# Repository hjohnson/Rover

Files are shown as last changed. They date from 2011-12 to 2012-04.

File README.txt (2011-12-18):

Introduction:
      This time, I'm presenting a whole robot, a project that has a slightly larger scale than my normal ones. This robot (or rover) was designed as an educational tool, a project to be built by teams of High School students over a period of 2-3 weeks. ÊAs such, the robot was designed for simplicity and durability, not low price. The robotÕs design is split into several modules: Mechanical Frame, Locomotion, Sensors, and Control. 

Mechanical Frame: 
	Material: The frame is constructed from four 1Ó width 80/20 extruded aluminum rails. For those who donÕt know, the 80/20 T-slot system is called Òthe industrial erector set,Ó and the description is fitting. The rails can be cut to size relatively easily with hand tools (though we use power tools,) and can be bolted together using aluminum plates, ÒT-nutsÓ and screws, instead of welding. This means that the system is easily reconfigurable on the fly, and small mistakes can be quickly remedied by loosening the plates and shifting the rail, instead of by removing welds.  
	Design: The main frame is a simple rectangle constructed from four lengths of 80/20 rail, bolted together at the corners with four triangular plates.  Attached to this main frame are several other lengths of rail. One houses the bumper; another houses the ball transport and vulnerability switch. (All of which will be discussed later) Three vertical stalks are also integrated into the design to hold other sensors. As a side bonus, these stalks are mounted firmly enough that the robot can technically be flipped upside down and rest on them, for easier service.

Locomotion:
	Mechanical Drive System: The robot incorporates two pneumatic wheels with integrated sprockets. The two wheels can rotate independently of each other, enabling steering, and are attached to a single axle, which is a 1/2-inch outside diameter tube. This axle is attached to the underside of the frame using pillow blocks.  Two 8-amp stepper motors drive the 2 wheels through a chain system. Sprockets attach to the motorsÕ drive shafts, and connect to the wheel-mounted sprockets through lengths of chain.  
	Motor Control System: A pair of Anaheim Automation MBC10101 Stepper Motor Drivers control the stepper motors. These drivers are powered by 24V provided by the robotÕs power unit, and have control inputs driven by the main control card. The main controls are: clock input, to determine the speed of the motors; Inhibit, to remove power from the motors and stop the robot; and Direction, to control the direction of rotation. These inputs are controlled by the main board, which will be discussed later. These drivers, while expensive, are from my experience highly reliable and are hard to burn, an excellent feature when wired by inexperienced builders who can easily miss a ground or clock signal. 
	Electrical Supply (power unit): The robotÕs power is provided by a custom supply based around two 12V, 2200mAh, Lead-Acid rechargeable batteries. When in Charge mode, the power supply wires these two batteries in parallel, each with their own 10 ohm ceramic power resistor, to the main power jack. While in this mode, ~14V can be supplied from an external regulated supply to charge the batteries. When in Drive mode, the power supply switches the two batteries into series, providing 24V output to the main power jack, which runs to the stepper motor drivers. The power supply also taps one of the batteries to supply 12V to a 7805 5V voltage regulator, which powers the control circuitry. Due to the power dissipation through this 7805, it is screwed to a Òheat sinkÓ (bottle cap). 

Sensors:
	The robot integrates several sensors to react to its surroundings. These include front-mounted bumper switches and phototransistors, and a rear-mounted vulnerability switch. 
	Bumper: A flexible bumper is attached to the front of the robot, along with 2 momentary lever switches. This enables the robot to detect when it has run into an object, usually the wall. The robotÕs response to this information can be determined in software by the students.
	Vulnerability Switch: A 3 position (SPTT) toggle switch is mounted to the rear of the robot, and acts as a manual shutdown switch and Òweak spot.Ó When the switch is positioned in the center (not connected), the robot operates normally. However, when the switch is actuated to either side, the robot instantly shuts down, turning off the motors and rendering the robot inoperable. This feature is implemented in software, but tampering with that section of code is forbidden. This switch is primarily used as a safety feature, but is also exploited for the high school competition, as bonus points are awarded to teams who can activate their opponentsÕ switches. 
	Phototransistors: While these are not currently attached, the phototransistors can be used to detect light levels, allowing the robots to navigate based on guidance from a flashlight, as well as to seek out the beacons above the competitionÕs Ògoals.Ó 

Control:
	At last, the more recognizable part. The robotÕs control system is remarkably simple, consisting of an Arduino-based card and an associated remote control.
	Control Card Hardware: 
      The actual circuitry on the card is remarkably simple, and primarily consists of an Arduino microprocessor, an XBee wireless transceiver, and some support circuitry.
       Motor Control: The Arduino output pins are buffered through 74LS14 hex inverters and then sent to the stepper motor drivers and the inputs from the bumper and vulnerability switches. The outputs are pulled up through resistors to 5V to ensure that the drivers are properly driven, as we had previously encountered problems where the ArduinoÕs output pins couldnÕt sufficiently drive the motor driversÕ input pins. 
      Sensors: The sensor inputs are buffered as well to form an extremely simple debouncing circuit. The Phototransistors also run through 1.5K resistors to ground, forming common collector amplifiers whose outputs run into the Analog In pins on the Arduino. 
      XBee: The control card utilizes an XBee wireless transceiver to enable bidirectional serial communication between the robot and the remote control. An Adafruit XBee Adapter kit is used to house the XBee and convert the ArduinoÕs 5V logic to the XBeeÕs 3.3V logic.  
	Control Card Software: 
      Motor Control: The top of the CardÕs priority list is controlling the motor drivers. Each of these drivers takes 3 inputs (clock, inhibit, and direction) as discussed previously. The 2 clock lines are driven by independent square waves generated by the Arduino Tone library. These square waves typically have frequencies between 2KHz and 5KHz.  Because the stepper motors have 200 steps/rotation, these speeds translate to motor speeds between 10 and 25 motor revolutions per second. However, due to the gearing present through the sprockets, the robotÕs wheels rotate at a lesser rate. (Embarrassingly, I havenÕt actually counted sprocket teeth or done the rest of this math yet. IÕll get back to you.) Inhibit and Direction, the other 2 data lines (per driver) are comparatively simple. When the driver sees a logic low on the inhibit pin, the motor is turned on, and when the driver sees a logic high, the motors are turned off. Similarly, for direction, logic low results in forward rotation, logic high results in backwards rotation. 
      Vulnerability Switch: The vulnerability switch input is monitored using an interrupt, whose interrupt service routine disables both motors, then waits for the vulnerability switch to be returned to center before exiting. In this way, the motors are disabled upon the switch being flicked, and will not re-enable, no matter what the user says, until the switch is returned to center.
      XBee Remote Control: To communicate through the XBee, a simple serial protocol is used, along with a pre-determined command set. Incoming serial bytes are read and interpreted by the program, with, for example, ÒWÓ signifying forward movement, ÒSÓ signifying backward movement, and ÒFÓ signifying stop. For more information about this process, look at the previous article, about the Remote Control designed to interface with this system.

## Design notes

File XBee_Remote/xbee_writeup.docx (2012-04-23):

This is a custom XBee-based remote control. The remote uses a 7-segment display, 7 buttons (plus a reset button), and 6 analog inputs as a user interface, and a 6-pin FTDI header for reprogramming through the Arduino IDE. Default code includes a program that prints the current state of the buttons to the XBee and a program that uses a switch statement to select what to send based on the buttons being pressed.

I originally designed this board for the Summer@Brown education program. In a class for this program, students design, construct, and program an aluminum-framed robot, and compete with it in a basic navigational challenge. Students have the option of controlling their robots remotely for part of the exercise. Previously, the control systems of these robots were created using discrete gates on 7400 series logic chips, and the remote control functionality was provided by expensive RF demo boards from Texas Instruments. I decided to upgrade the systems by implementing an Arduino and XBee based control system on the robots. That way, the robots could be controlled by anything that could speak over a serial connection. I had the students build their own remote controls on a breadboard, but quickly found that the wires would pop out and the systems would break. To fix the problem, I designed this remote control. Students would still solder it together and program it, but it would be easier to hold, have more buttons, and be more reliable. Further, it would be expandable: If they outstripped the 7 switches, they could always attach more switches, potentiometers, or I2C communications devices through the analog lines.

While I designed this board to be paired with a control system mounted on a robot, it can be used to interface with anything that communicates over an XBee serial connection. As such, it could work as both a remote control and a remote monitoring system. The Atmega328P runs off 5 volts, while the XBee runs of 3.3 volts. To convert between the two, a low drop out regulator is used, along with a 74AHC125 buffer. However, the '125 has another useful feature. Using its active-low Output Enable pin, its outputs switched to High Impedance at will. Since the buffer is used on both the RX and TX lines, the Atmega328P can disconnect itself from the XBee.

Typically, when Arduinos and XBees are combined, the XBee cannot be connected to the Arduino during serial bootloading. To solve this problem, designers usually put in a DPDT switch to manually transition between connecting the Atmega328 to the computer and connecting it to the outside world. However, since the Atmega I/O lines are high impedance during reset and bootloading, I simply connect the ‘125 Output Enable pin to the Atmega, and install a pull-up resistor on the line. This means that during bootloading, the Atmega is disconnected from the XBee. When the program is loaded and the Atmega is ready to communicate wirelessly, it simply pulls the Output Enable pin low.

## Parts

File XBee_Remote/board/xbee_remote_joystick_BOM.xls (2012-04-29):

Digi-Key Part Number | Manufacturer | Manufacturer Part Number | Quantity 1 | Description | Comments
ATMEGA328-PU-ND | ATMEL | ATMEGA328-PU | 1 | IC MCU AVR 32K FLASH 28PDIP
568-1393-5-ND | NXP SEMICONDUCTORS | 74HC125N,652 | 1 | IC BUFFER DVR TRI-ST QD 14PDIP
568-1484-5-ND | NXP SEMICONDUCTORS | 74HC595N,112 | 1 | IC SHIFT REGISTER 8BIT 16DIP
296-21633-5-ND | TEXAS INSTRUMENTS | UA78M33CKCS | 1 | IC POS-V REG 500MA 3.3V TO220-3 | 3.3V regulator
160-1708-ND | LITE-ON INC | LTL-1CHE | 2 | LED 3MM HI-EFF RED DIFFUSED
X908-ND | ECS INC | ZTT-16.00MX | 1 | CER RESONATOR 16.00MHZ
150QBK-ND | YAGEO | CFR-25JB-52-150R | 2 | RES 150 OHM 1/4W 5% CARBON FILM | Can swap resistors, caps for generics, etc
1.0KQBK-ND | YAGEO | CFR-25JB-52-1K | 1 | RES 1.0K OHM 1/4W 5% CARBON FILM
10KQBK-ND | YAGEO | CFR-25JB-52-10K | 3 | RES 10K OHM 1/4W 5% CARBON FILM
399-4151-ND | KEMET | C315C104M5U5TA | 3 | CAP CER 0.1UF 50V 20% RADIAL
P966-ND | PANASONIC - ECG | ECE-A1CKS100 | 1 | CAP ALUM 10UF 16V 20% RADIAL
P5165-ND | PANASONIC - ECG | ECA-1VM101 | 1 | CAP ALUM 100UF 35V 20% RADIAL
A98036-ND | TE CONNECTIVITY AMP | 1776275-2 | 1 | TERM BLOCK 2POS SIDE ENT 3.5MM
A26509-40-ND | TE CONNECTIVITY AMP | 4-103741-0 | 1 | CONN HDR BRKWAY .100 40POS VERT
S5751-10-ND | SULLINS CONNECTOR SOLUTIONS | NPPN101BFCN-RC | 2 | CONN RECEPT 2MM SINGLE STR 10POS | Xbee headers
EG1903-ND | E-SWITCH | EG1218 | 1 | SWITCH SLIDE SPDT 30V.2A PC MNT
EG2513-ND | E-SWITCH | TL1107BF180WQ | 7 | SWITCH TACTILE SPST-NO 0.05A 12V
In addition:
Sparkfun 7-segment, COM-08546
Sparkfun Thumb Joystick, COM-09032

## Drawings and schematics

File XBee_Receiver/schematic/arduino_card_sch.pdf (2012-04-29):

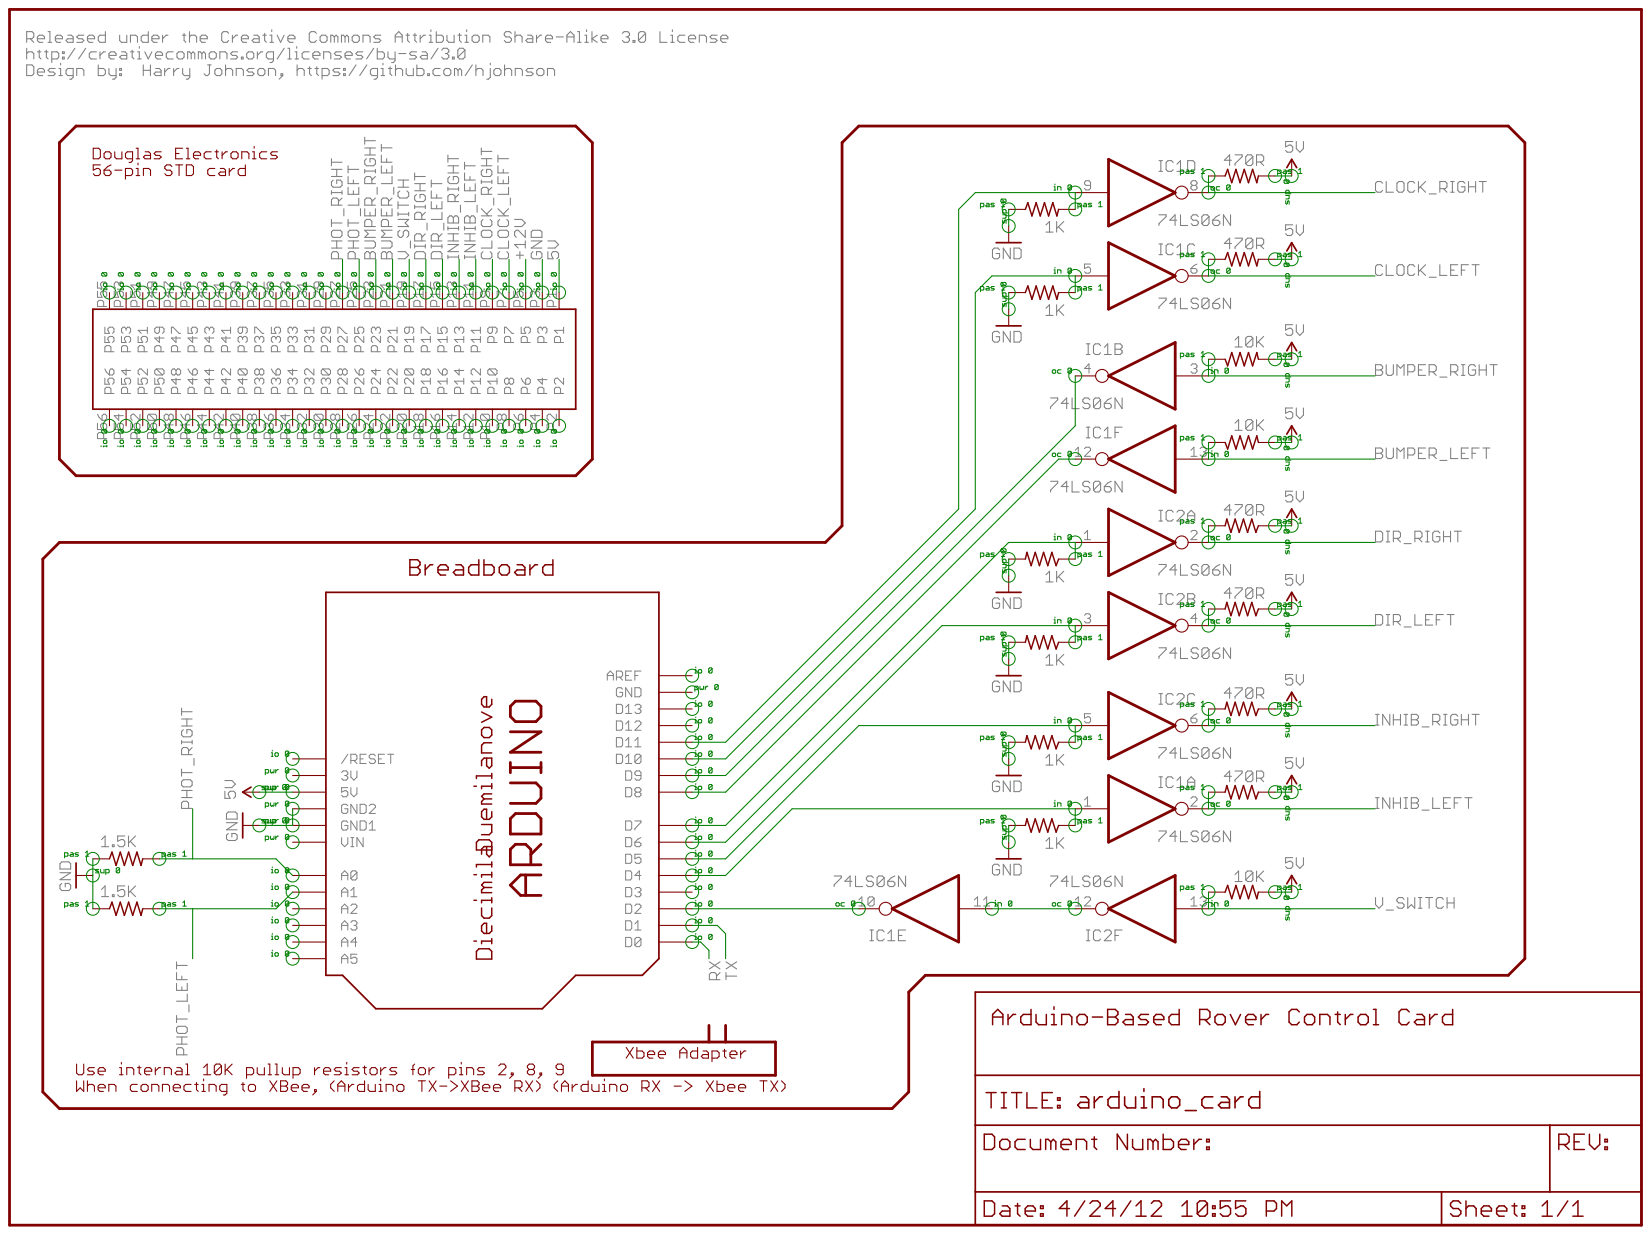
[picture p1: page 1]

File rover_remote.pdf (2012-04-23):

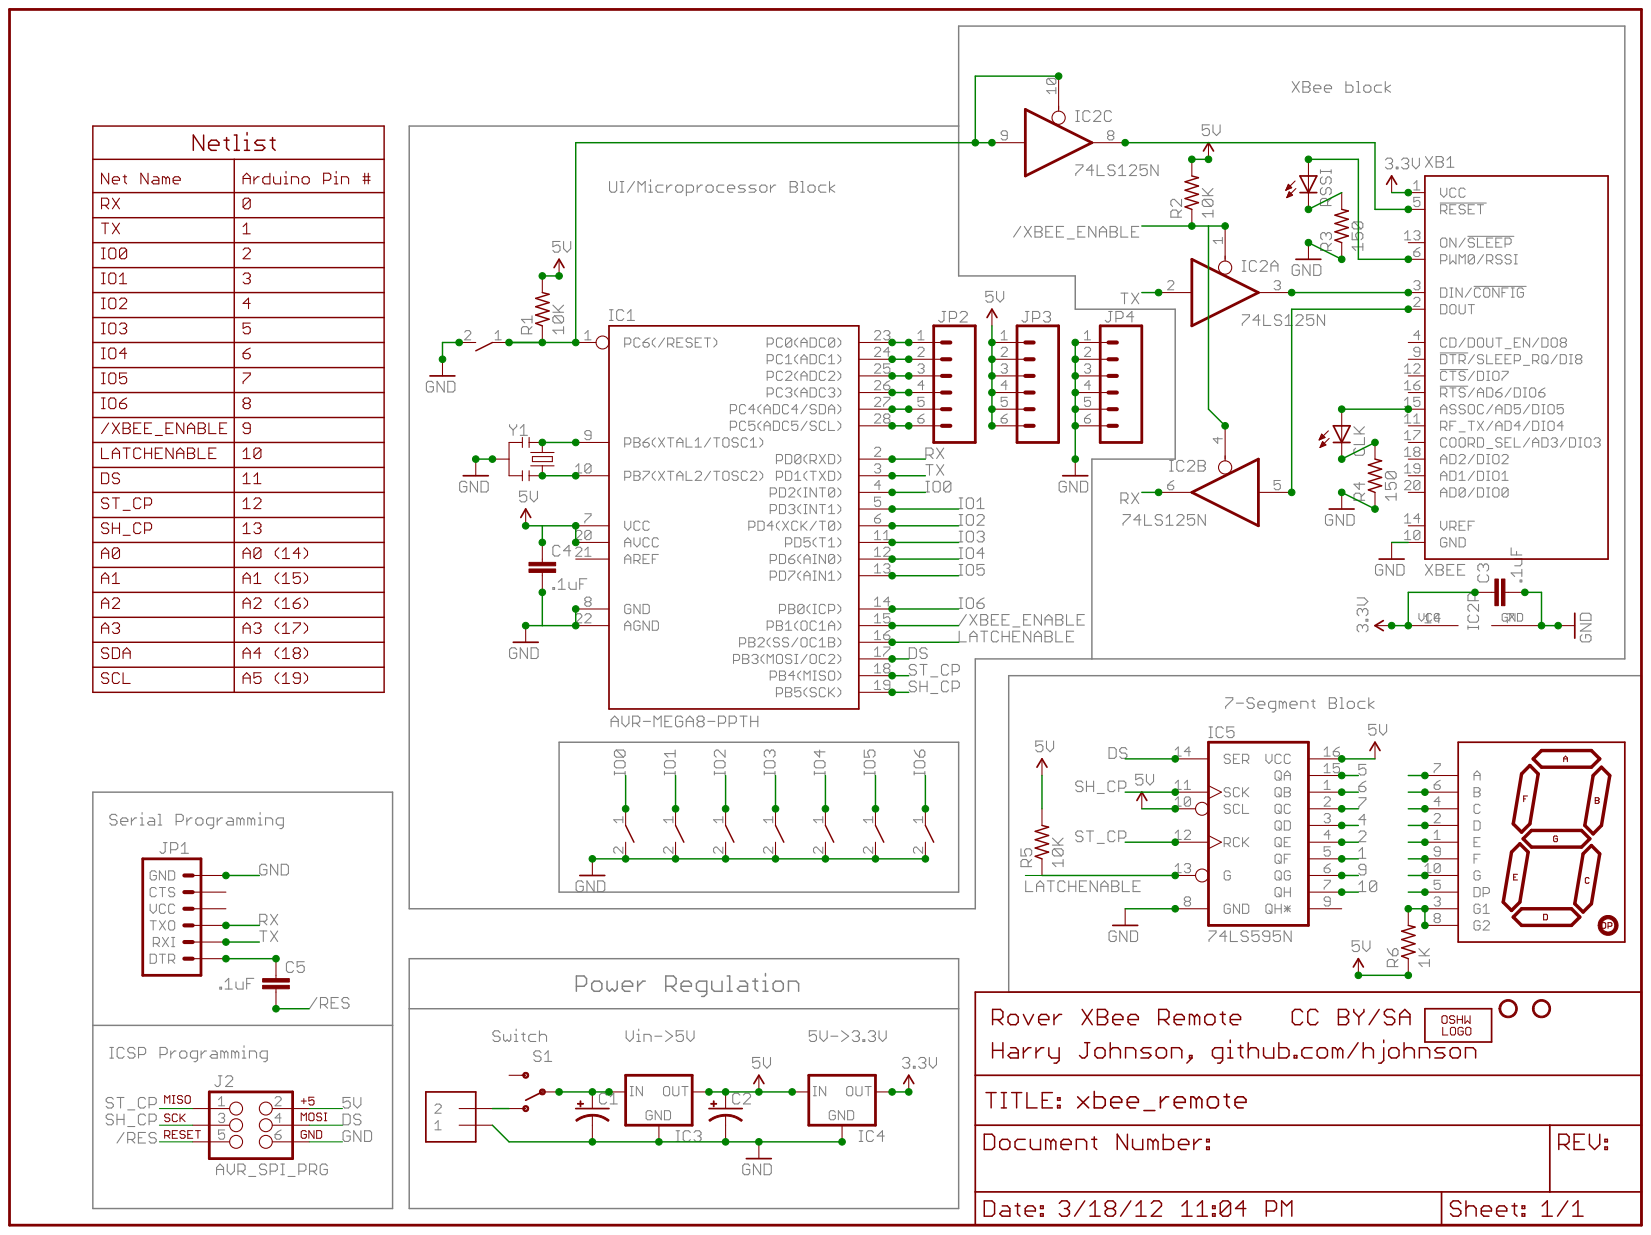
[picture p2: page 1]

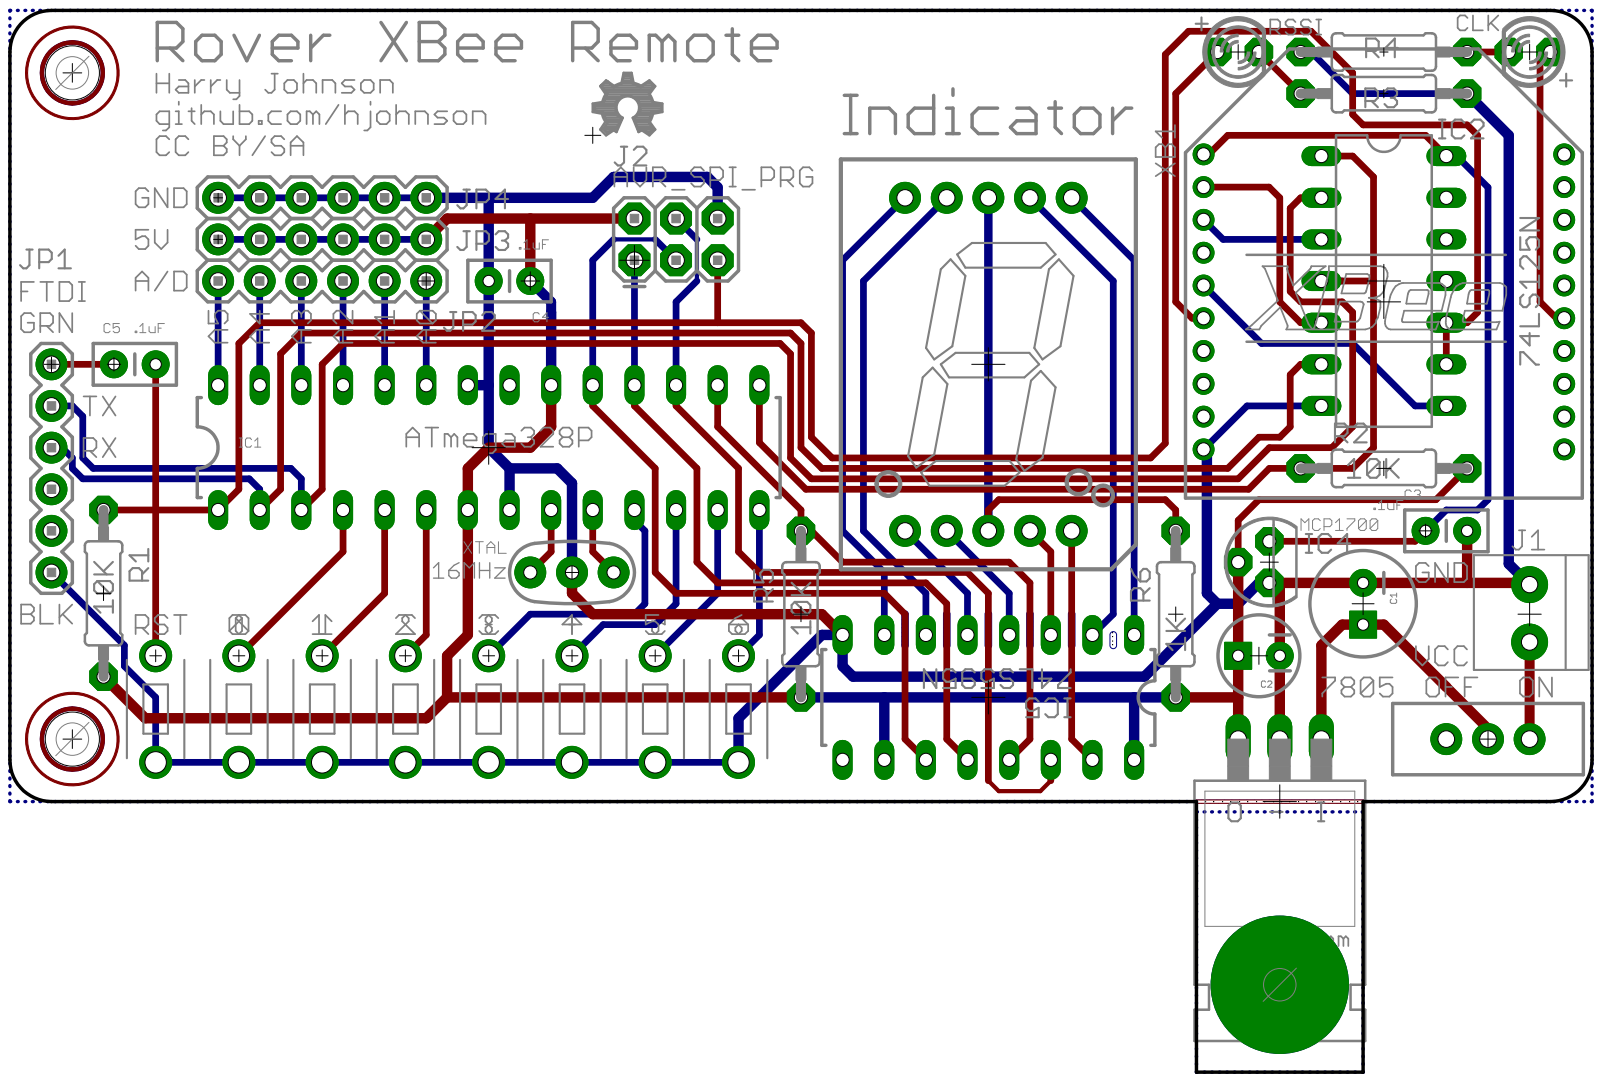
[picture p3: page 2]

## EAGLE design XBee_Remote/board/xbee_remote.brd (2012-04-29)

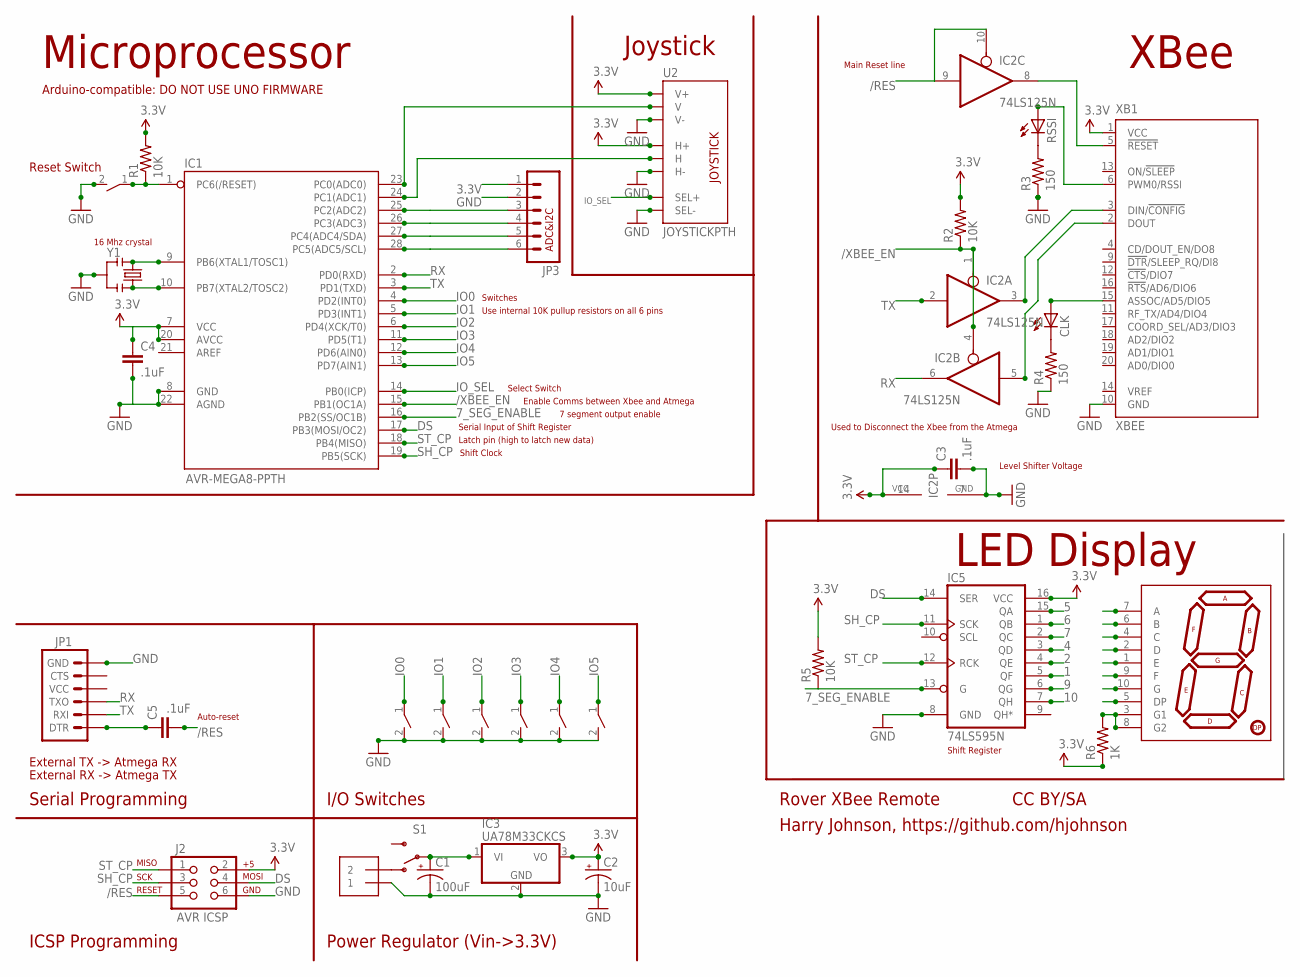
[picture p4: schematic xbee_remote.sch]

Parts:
C1: 100uF; CPOL-RADIAL-100UF-25V
C2: 10uF; CPOL-RADIAL-10UF-25V
C3, C4, C5: .1uF; CAP-PTH-SMALL2
CLK: LED3MM
IC1: AVR-MEGA8-PPTH; DIL28-3
IC2: 74LS125N; DIL14
IC3: UA78M33CKCS; TO220V
IC5: 74LS595N; DIL16
J1: 1X2-3.5MM; 3.5MMTERM
J2: AVR ICSP; 2X3
JP1: ARDUINO_SERIAL_PROGRAMPTH; 1X06
JP3: M06SIP; 1X06
R1, R2, R5: 10K; 0207/10
R3, R4: 150; 0207/10
R6: 1K; 0207/10
RSSI: LED3MM
S1: SWITCH-SPSTPTH; SWITCH-SPDT
U2: JOYSTICKPTH; JOYSTICK
U$4: 7-SEGMENT-DISPLAY-1"-RED; 7-SEGMENT-1"PTH
U$8, U$9, U$10, U$11, U$12, U$13, U$14: TACT_TL1107
XB1: XBEE
Y1: RESONATORPTH; RESONATOR-PTH

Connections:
1: IC5.5 (QF), U$4.1 (E)
2: IC5.4 (QE), U$4.2 (D)
3.3V: C2.1 (+), C3.1, C4.1, IC1.7 (VCC), IC1.20 (AVCC), IC2.14 (VCC), IC3.3 (VO), IC5.16 (VCC), J2.2, JP3.1, R1.2, R2.2, R5.2, R6.1, U2.H1 (H+), U2.V1 (V+), XB1.1 (VCC)
3V3_/RST: IC2.8 (O), XB1.5 (!RESET)
3V3_RX: IC2.5 (I), XB1.2 (DOUT)
3V3_TX: IC2.3 (O), XB1.3 (DIN/!CONFIG)
4: IC5.3 (QD), U$4.4 (C)
5: IC5.15 (QA), U$4.5 (DP)
6: IC5.1 (QB), U$4.6 (B)
7: IC5.2 (QC), U$4.7 (A)
7_SEG_ENABLE: IC1.16 (PB2(SS/OC1B)), IC5.13 (G), R5.1
9: IC5.6 (QG), U$4.9 (F)
10: IC5.7 (QH), U$4.10 (G)
/RES: C5.2, IC1.1 (PC6(/RESET)), IC2.9 (I), IC2.10 (OE), J2.5, R1.1, U$8.1
/XBEE_EN: IC1.15 (PB1(OC1A)), IC2.1 (OE), IC2.4 (OE), R2.1
A2: IC1.25 (PC2(ADC2)), JP3.3
A3: IC1.26 (PC3(ADC3)), JP3.4
DS: IC1.17 (PB3(MOSI/OC2)), IC5.14 (SER), J2.4
GND: C1.2 (-), C2.2 (-), C3.2, C4.2, IC1.8 (GND), IC1.22 (AGND), IC2.7 (GND), IC3.2 (GND), IC5.8 (GND), J1.1, J2.6, JP1.6 (GND), JP3.2, R3.1, R4.1, U2.B2A (SEL-), U2.H3 (H-), U2.V3 (V-), U$8.2, U$9.2, U$10.2, U$11.2, U$12.2, U$13.2, U$14.2, XB1.10 (GND), Y1.2
IO0: IC1.4 (PD2(INT0)), U$9.1
IO1: IC1.5 (PD3(INT1)), U$10.1
IO2: IC1.6 (PD4(XCK/T0)), U$11.1
IO3: IC1.11 (PD5(T1)), U$12.1
IO4: IC1.12 (PD6(AIN0)), U$13.1
IO5: IC1.13 (PD7(AIN1)), U$14.1
IO_SEL: IC1.14 (PB0(ICP)), U2.B1A (SEL+)
unnamed: IC1.9 (PB6(XTAL1/TOSC1)), Y1.1
unnamed: IC1.10 (PB7(XTAL2/TOSC2)), Y1.3
unnamed: J1.2, S1.1 (O)
unnamed: C5.1, JP1.1 (DTR)
unnamed: R6.2, U$4.3 (G1), U$4.8 (G2)
unnamed: RSSI.A, XB1.6 (PWM0/RSSI)
unnamed: R3.2, RSSI.K (C)
unnamed: CLK.A, XB1.15 (ASSOC/AD5/DIO5)
unnamed: CLK.K (C), R4.2
RX: IC1.2 (PD0(RXD)), IC2.6 (O), JP1.3 (TXO)
SCL: IC1.28 (PC5(ADC5/SCL)), JP3.6
SDA: IC1.27 (PC4(ADC4/SDA)), JP3.5
SH_CP: IC1.19 (PB5(SCK)), IC5.11 (SCK), J2.3
ST_CP: IC1.18 (PB4(MISO)), IC5.12 (RCK), J2.1
TX: IC1.3 (PD1(TXD)), IC2.2 (I), JP1.2 (RXI)
VIN: C1.1 (+), IC3.1 (VI), S1.2
VIN_H: IC1.24 (PC1(ADC1)), U2.H2 (H)
VIN_V: IC1.23 (PC0(ADC0)), U2.V2 (V)

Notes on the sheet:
LED Display
Serial Programming
Microprocessor
Rover XBee Remote
Harry Johnson, https://github.com/hjohnson
CC BY/SA
ICSP Programming
Power Regulator (Vin->3.3V)
XBee
Shift Clock
Latch pin (high to latch new data)
Serial Input of Shift Register
7 segment output enable
Enable Comms between Xbee and Atmega
Select Switch
ADC&I2C
External TX -> Atmega RX
External RX -> Atmega TX
I/O Switches
Joystick
Switches
Use internal 10K pullup resistors on all 6 pins
16 Mhz crystal
Main Reset line
Used to Disconnect the Xbee from the Atmega
Auto-reset
Reset Switch
Arduino-compatible: DO NOT USE UNO FIRMWARE
Level Shifter Voltage
Shift Register

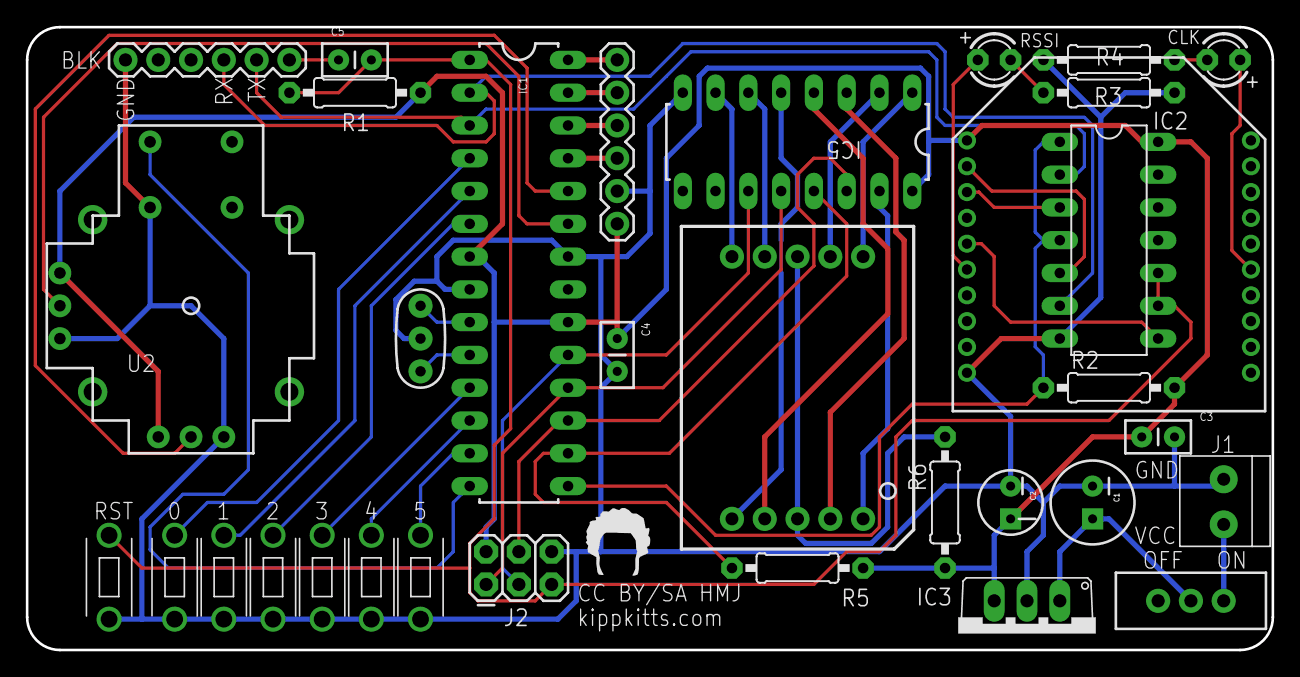
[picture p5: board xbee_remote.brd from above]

Board: 2 copper layers, 96.5 x 48.3 mm, 34 parts (0 on the bottom side), 44 nets.

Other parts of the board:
U$2: TOP_DOCU_5MM

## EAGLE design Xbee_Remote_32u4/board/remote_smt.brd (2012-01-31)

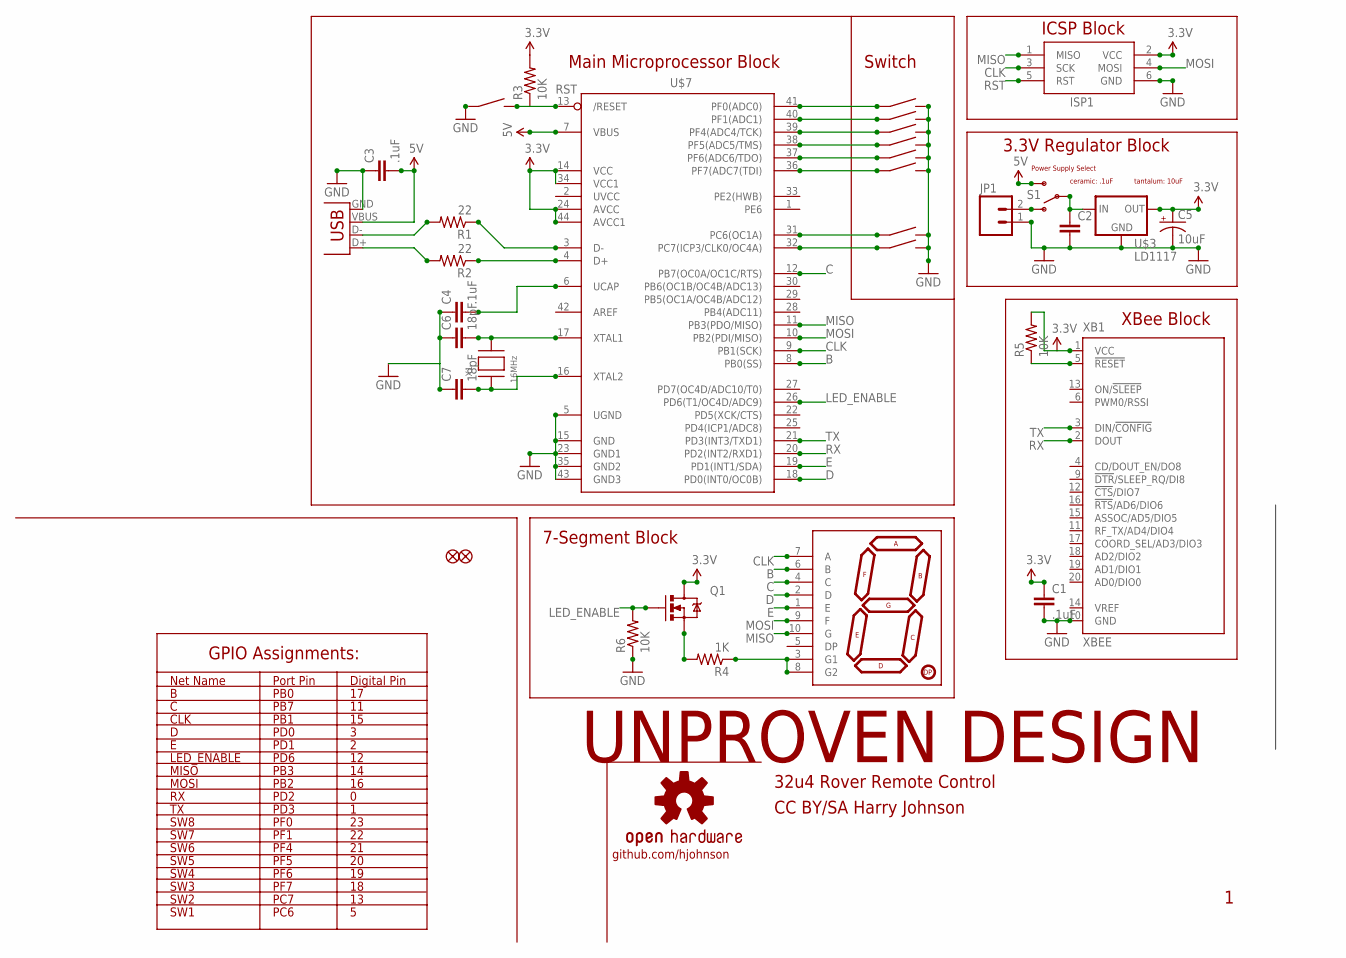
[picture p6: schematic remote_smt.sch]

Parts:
C1, C3, C4: .1uF; 0805
C2: CAP0805; 0805
C5: 10uF; EIA3528-KIT
C6, C7: 18pF; 0805
ISP1: AVRISP-6; AVRISP
JP1: M023.5MM; SCREWTERMINAL-3.5MM-2
JP2, JP3: FIDUCIAL1.5X3; FIDUCIAL-1.5X3
Q1: MOSFET-NCHANNELSMD; SOT23-3
R1, R2: 22; 0805
R3, R5, R6: 10K; 0805
R4: 1K; 0805
S1: SWITCH-SPSTKIT; SWITCH-SPDT_KIT
U$1: 7-SEGMENT-DISPLAY-1"-RED; 7-SEGMENT-1"PTH
U$2, U$6, U$8, U$11, U$12, U$13, U$14, U$15, U$17: SPST_SWITCH; EG2513-ND
U$3: LD1117; SOT223
U$7: ATMEGA32U4-AU; TQFP44
U$10: OSHW-LOGOL; OSHW-LOGO-L
X1: 16MHz; NX5032
X2: USBPTH; USB-B-PTH
XB1: XBEE

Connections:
3.3V: C1.1, C5.A (+), ISP1.2 (VCC), Q1.3 (D), R3.2, R5.2, U$3.2 (OUT), U$7.14 (VCC), U$7.24 (AVCC), U$7.34 (VCC1), U$7.44 (AVCC1), XB1.1 (VCC)
5V: C3.2, S1.3 (S), U$7.7 (VBUS), X2.VBUS
B: U$1.6 (B), U$7.8 (PB0(SS))
C: U$1.4 (C), U$7.12 (PB7(OC0A/OC1C/RTS))
CLK: ISP1.3 (SCK), U$1.7 (A), U$7.9 (PB1(SCK))
D: U$1.2 (D), U$7.18 (PD0(INT0/OC0B))
E: U$1.1 (E), U$7.19 (PD1(INT1/SDA))
GND: C1.2, C2.2, C3.1, C4.1, C5.C (-), C6.1, C7.1, ISP1.6 (GND), JP1.1, R6.1, U$2.P$1 (1), U$3.1 (GND), U$3.4 (GND), U$6.P$2 (2), U$7.5 (UGND), U$7.15 (GND), U$7.23 (GND1), U$7.35 (GND2), U$7.43 (GND3), U$8.P$2 (2), U$11.P$2 (2), U$12.P$2 (2), U$13.P$2 (2), U$14.P$2 (2), U$15.P$2 (2), U$17.P$2 (2), X2.GND, XB1.10 (GND)
LED_ENABLE: Q1.1 (G), R6.2, U$7.26 (PD6(T1/OC4D/ADC9))
MISO: ISP1.1 (MISO), U$1.10 (G), U$7.11 (PB3(PDO/MISO))
MOSI: ISP1.4 (MOSI), U$1.9 (F), U$7.10 (PB2(PDI/MISO))
unnamed: C6.2, U$7.17 (XTAL1), X1.P$2
unnamed: C7.2, U$7.16 (XTAL2), X1.P$1
unnamed: R1.1, U$7.3 (D-)
unnamed: R2.1, U$7.4 (D+)
unnamed: R2.2, X2.D+
unnamed: R1.2, X2.D-
unnamed: R4.1, U$1.3 (G1), U$1.8 (G2)
unnamed: C4.2, U$7.6 (UCAP)
unnamed: Q1.2 (S), R4.2
unnamed: JP1.2, S1.1 (O)
unnamed: C2.1, S1.2, U$3.3 (IN)
RST: ISP1.5 (RST), R3.1, U$2.P$2 (2), U$7.13 (/RESET)
RX: U$7.20 (PD2(INT2/RXD1)), XB1.2 (DOUT)
SW1: U$6.P$1 (1), U$7.31 (PC6(OC1A))
SW2: U$7.32 (PC7(ICP3/CLK0/OC4A)), U$8.P$1 (1)
SW3: U$7.36 (PF7(ADC7(TDI)), U$17.P$1 (1)
SW4: U$7.37 (PF6(ADC6/TDO)), U$15.P$1 (1)
SW5: U$7.38 (PF5(ADC5/TMS)), U$14.P$1 (1)
SW6: U$7.39 (PF4(ADC4/TCK)), U$13.P$1 (1)
SW7: U$7.40 (PF1(ADC1)), U$12.P$1 (1)
SW8: U$7.41 (PF0(ADC0)), U$11.P$1 (1)
TX: U$7.21 (PD3(INT3/TXD1)), XB1.3 (DIN/!CONFIG)
XBEE_RST: R5.1, XB1.5 (!RESET)

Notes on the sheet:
Net Name
Digital Pin
CLK
LED_ENABLE
MISO
MOSI
Port Pin
PB0
PB7
PB1
PD0
PD1
PD6
PB3
PB2
PD2
PD3
SW8
SW7
SW6
SW5
SW4
SW3
SW2
SW1
PF0
PF1
PF4
PF5
PF6
PF7
PC7
PC6
GPIO Assignments:
3.3V Regulator Block
ICSP Block
XBee Block
7-Segment Block
Main Microprocessor Block
Switch

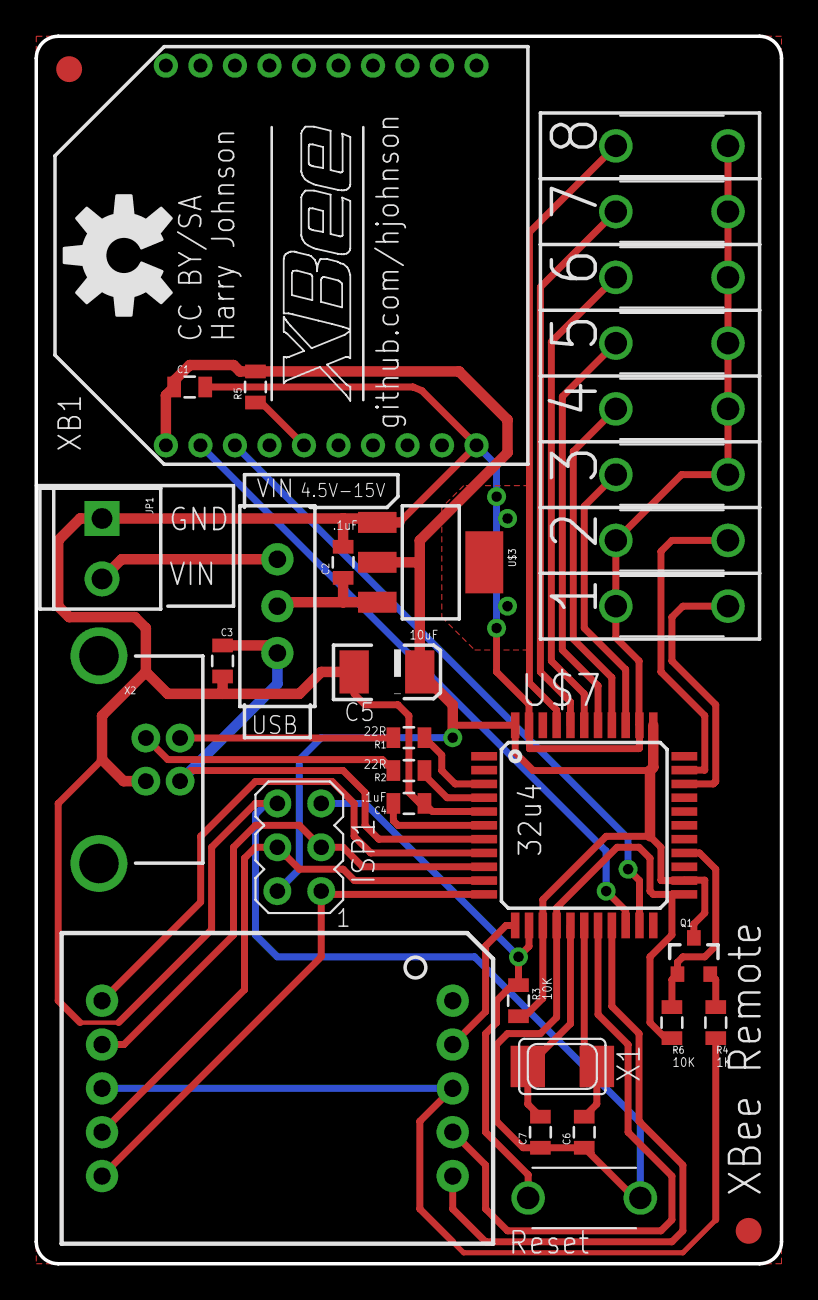
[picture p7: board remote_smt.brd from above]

Board: 2 copper layers, 43.2 x 71.1 mm, 35 parts (0 on the bottom side), 34 nets.

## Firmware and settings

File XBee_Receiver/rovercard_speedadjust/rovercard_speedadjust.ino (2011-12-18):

//rovercard_speedadjust: the whole hog. Bumpers, Remote Control, Phototransistors
#include <Tone.h> //tone functions, allows output of square waves

const int INHIB_LFT = 4; //ON-OFF left, when LOW, motors inhibited
const int INHIB_RGHT = 5; //ON-OFF right, when LOW, motors inhibited
const int DIR_LFT = 6; //direction left, when HIGH, motor reversed
const int DIR_RGHT = 7; //direction right, when HIGH, motor reversed
const int LVR_LFT = 8; //bumper switch left, high when pressed
const int LVR_RGHT = 9; //bumper switch right, high when pressed
const int PHOT_LFT = 1; //phototransistor left, analog pin 1
const int PHOT_RGHT = 0; //phototransistor right, analog pin 0
const int V_SWTCH = 2; //vulnerability switch
const int CLK_LFT = 10; //clock output left
const int CLK_RGHT = 11; //clock output right

char tmpRead = ' ';  //temporary serial value 
int user_stopped = 0; //has the user stopped the rover using the remote?
unsigned int speedL = 3000;
unsigned int speedR = 3000;
Tone velocityL; //actually speed of left
Tone velocityR; //actually speed of right

const int thet_diff_LO =  -150; //
const int thet_diff_HI = 150; //
const int thet_summ_LO =  175; 
const int thet_summ_HI =  1000; //4 volts.

int summ = 0;
int diff = 0;
int photReadLFT = 0;
int photReadRGHT = 0;
int lvr_enabled = 1;

void setup() {
  Serial.begin(9600);
  for(int ii =4; ii<=11; ii++) {
    pinMode(ii, OUTPUT);   //set up all of the inhibs, clock, etc as output
  }
  pinMode(V_SWTCH, INPUT); //V switch input
  pinMode(LVR_LFT, INPUT);
  pinMode(LVR_RGHT, INPUT);
   digitalWrite(V_SWTCH, LOW); //enable internal pullup.
  digitalWrite(LVR_LFT, HIGH);
  digitalWrite(LVR_RGHT, HIGH);
  
  velocityL.begin(CLK_LFT); //set up frequency output pins. don't need to do this again
  velocityR.begin(CLK_RGHT); 
  velocityL.play(speedL);  //3KHz square wave 
  velocityR.play(speedR); //3Khz square wave. These are changeable live, just be careful.
  
  digitalWrite(INHIB_LFT, LOW); //inhibit both motors
  digitalWrite(INHIB_RGHT, LOW);
  user_stopped = 1;
  attachInterrupt(0, interruptroutine, LOW);  //when the V-switch is flicked to the side, call interruptroutine function

}

void loop() {
  if(Serial.available()>0) {
    tmpRead = Serial.read();
    switch(tmpRead) {
   
      case 'F': 
      digitalWrite(INHIB_LFT, LOW); 
      digitalWrite(INHIB_RGHT, LOW);
     user_stopped = 1; 
      break; //turns off both motors
   
    case 'W': 
      digitalWrite(INHIB_LFT, HIGH); 
      digitalWrite(INHIB_RGHT, HIGH); 
      digitalWrite(DIR_LFT, LOW); 
      digitalWrite(DIR_RGHT, LOW); 
      user_stopped = 0;
      break; //forward
    
    case 'S': 
      digitalWrite(INHIB_LFT, HIGH); 
      digitalWrite(INHIB_RGHT, HIGH); 
      digitalWrite(DIR_LFT, HIGH); 
      digitalWrite(DIR_RGHT, HIGH); 
      user_stopped = 0;
      break; //backward
    
    case 'A': 
       digitalWrite(INHIB_LFT, HIGH);
       digitalWrite(INHIB_RGHT, LOW); //disable the right motor 
       digitalWrite(DIR_LFT, HIGH); 
       digitalWrite(DIR_RGHT, HIGH); 
       user_stopped = 0;
       break;
       
       case 'D': 
       digitalWrite(INHIB_LFT, LOW); //disable the left motor 
       digitalWrite(INHIB_RGHT, HIGH);
       digitalWrite(DIR_LFT, HIGH); 
       digitalWrite(DIR_RGHT, HIGH); //back up.
       user_stopped = 0;
       break;
       
    case 'T': 
      speedL += 500;
      speedR += 500;
      Serial.print("Left: ");
      Serial.println(speedL);
      Serial.print("Right: ");
      Serial.println(speedR);
      velocityL.play(speedL);  
      velocityR.play(speedR);
    break;
    
     case 'Y': 
      speedL -= 500;
      speedR -= 500;
      Serial.print("Left: ");
      Serial.println(speedL);
      Serial.print("Right: ");
      Serial.println(speedR);
      velocityL.play(speedL);  
      velocityR.play(speedR);
    break;
    
      case 'U': lvr_enabled = 0; break;
      case 'I': lvr_enabled = 1; break;
    
    default: 
      break;
    } 
  }
  if((digitalRead(LVR_LFT)==HIGH) && (user_stopped ==0) && (lvr_enabled == 1)) {
   Serial.println("Left Lever"); 
      digitalWrite(DIR_LFT, HIGH); //back up 
      digitalWrite(DIR_RGHT, HIGH); 
      delay(750);
      digitalWrite(DIR_LFT, LOW);  //turn right
     delay(500);
     digitalWrite(DIR_RGHT, LOW); //go back to going forward.
    
  }
  
   if((digitalRead(LVR_RGHT)==HIGH) && (user_stopped ==0) && (lvr_enabled ==1)) {
   Serial.println("Right Lever"); 
      digitalWrite(DIR_LFT, HIGH); //back up
      digitalWrite(DIR_RGHT, HIGH); 
      delay(750);
      digitalWrite(DIR_RGHT, LOW); //turn left
     delay(500);
     digitalWrite(DIR_LFT, LOW); //back to going forward
  }
  
  if(user_stopped == 0) { //Phototransistor code
   photReadLFT = analogRead(PHOT_LFT); //read left phototransistor, 0-1023
   photReadRGHT= analogRead(PHOT_RGHT); //right phototransistor.
   summ = photReadLFT + photReadRGHT; //sum of two values
   diff = photReadLFT - photReadRGHT; //difference of two values
   Serial.print("Sum: ");
   Serial.println(summ);
   Serial.print("Diff: ");
   Serial.println(diff);
   if((summ < thet_summ_HI) && (summ > thet_summ_LO)) { //if the sum is too low, the rover is too far away to care, if the sum is too high, the robot is too close to care.
     
     if(diff < thet_diff_LO) { //if the robot is skewed too far to the left.
       Serial.println("turning right"); 
       digitalWrite(INHIB_RGHT, LOW); //turn off right motor, robot turns right.
       while(diff < thet_diff_LO) { //wait until centered. 
         photReadLFT = analogRead(PHOT_LFT); //updating constantly.
         photReadRGHT= analogRead(PHOT_RGHT);
         diff = photReadLFT - photReadRGHT;
       }
       digitalWrite(INHIB_RGHT, HIGH); //go back to going forward.
       Serial.println("Going Forward");
     }
     
      if(diff > thet_diff_HI) { //robot is skewed too far to the right 
       digitalWrite(INHIB_LFT, LOW);  //turn left.
       while(diff > thet_diff_HI) { //until centered
         photReadLFT = analogRead(PHOT_LFT);
         photReadRGHT= analogRead(PHOT_RGHT);
         diff = photReadLFT - photReadRGHT;
       } 
       digitalWrite(INHIB_LFT, HIGH); //go forward.
       Serial.println("Going Forward");
     } 
   }    
  }
}

void interruptroutine() { // V-switch activated!
  digitalWrite(4, LOW); //turn off left motor
  digitalWrite(5, LOW); //turn off right motor
  while(digitalRead(2) == LOW) { //loop until V-switch toggled to center
  } 
}

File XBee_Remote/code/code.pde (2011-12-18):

/*
XBee Remote, code
By Harry Johnson
This file is part of Xbee Remote
 
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
Reference:

 Pin Assignments:
 0: RX
 1: TX
 2: Switch 0
 3: Switch 1
 4: Switch 2
 5: Switch 3
 6: Switch 4
 7: Switch 5
 8: XBee Comm enable, active low.
 9: Switch 6
 10: LED Latch Enable, not on the SPI bus.
 11: Latch DS, data pin
 12: Latch ST_CP Latchpin
 13: Latch SH_CP clockPin.
 
 Seven Segment Assignments
 Q0: Decimal, LSB
 Q1: B
 Q2: A
 Q3: C
 Q4: D
 Q5: E
 Q6: F
 Q7: G, MSB
 
 EEPROM:
 0: LSB of PAN ID.
 1: MSB of PAN ID.
 
 Switch Assignments: 
 none: stop.
 0: Forward
 1: Backward
 */
#include <EEPROM.h> //to store XBee information.
byte XBeeAddress[2];
byte segVal[16];
byte latchPin = 12;
static byte clockPin = 13;
static byte dataPin = 11;

byte robotState = -1; //0: stopped. 1: forward. 2: backward.
int pinValues = 0;

//Utility methods. You shouldn't have to modify these.
void displayValue(int value) {
  displayRawValue(segVal[value]);
}

void displayRawValue(byte value) {
  digitalWrite(latchPin, LOW); //keep the LEDs from updating while data is being shifted.
  shiftOut(dataPin, clockPin, MSBFIRST, value); //shift out all the data.
  digitalWrite(latchPin, HIGH); //update the LEDs.
}

void segSetup() { //The various 7 segment characters.
  segVal[0]   = ~0x7F; //~01111111
  segVal[1]   = ~0x0A; //~00001010
  segVal[2]   = ~0xB6; //~10110110
  segVal[3]   = ~0x9E; //~10011110
  segVal[4]   = ~0xCA; //~11001010
  segVal[5]   = ~0xDC; //~11011100
  segVal[6]   = ~0xFC; //~11111100
  segVal[7]   = ~0x0E; //~00001110
  segVal[8]   = ~0xFE; //~11111110
  segVal[9]   = ~0xCE; //~11001110
  segVal[0xA] = ~0xEF; //~11101111
  segVal[0xB] = ~0xF9; //~11111001
  segVal[0xC] = ~0x75; //~01110101
  segVal[0xD] = ~0xBB; //~10111011
  segVal[0xE] = ~0xF5; //~11110101
  segVal[0xF] = ~0xE5; //~11100101
 pinMode(8, OUTPUT);
  pinMode(10, OUTPUT);
  pinMode(11, OUTPUT);
  pinMode(12, OUTPUT);
  pinMode(13, OUTPUT);
  digitalWrite(10, LOW); //enable the whole LCD system. (had to be off since it shares the SPI bus, just in case. Need to redefine SS, though) 
  digitalWrite(latchPin, HIGH);
  displayValue(0xA);
}

//XBee Code
void getPAN_EEPROM() {
  XBeeAddress[0] = EEPROM.read(0);
  XBeeAddress[1] = EEPROM.read(1);
}

void setPAN_EEPROM(word value) {
  XBeeAddress[0] = lowByte(value);
  XBeeAddress[1] = highByte(value);
  EEPROM.write(0, XBeeAddress[0]);
  delay(4); //write takes 3.3ms to complete.
  EEPROM.write(1, XBeeAddress[1]);
  delay(4);
}

void resetPAN() {
  setPAN_EEPROM(0x3332);
  setPAN_XBEE(); 
}

void setPAN_XBEE() {
  enableXBee();
  Serial.begin(9600);
  Serial.print("+++");
  delay(5);
  Serial.print("ATID");
  Serial.print(word(XBeeAddress[1], XBeeAddress[0]), HEX);
  delay(5);
  Serial.print("ATWR");
  delay(5);
  disableXBee();
}

void enableXBee() {
  digitalWrite(8, LOW); //enable XBee communications.
  delay(1);
}

void disableXBee() {
  digitalWrite(8, HIGH); //enable XBee communications.
  delay(1);
}



unsigned int getPins() { //easy way to do switch statements based on pin states. Not required, though.
  unsigned int result =0;
  for(int ii = 0; ii<=5; ii++) {
    result |= ((1-(digitalRead(ii+2))) << ii); //if pin is HIGH (1), then activate appropriate bit.
  }
  result |= ((1-digitalRead(9)) << 6); //handling the straggler.
  return result;
}

//end of utility methods.

//Program here!
void setup() {
  Serial.begin(9600); //XBee uses 9600.
  Serial.flush(); //clear input buffer.
  disableXBee(); //tri-state the pins.

  segSetup(); //setup the segment values, etc. 
  for(byte ii = 2; ii<=7; ii++) { //switches 0-5 inputs.
    pinMode(ii, INPUT); //input
    digitalWrite(ii, HIGH); //internal pullups enabled.
  }
  pinMode(9, INPUT); //switch 6 input
  digitalWrite(9, HIGH);//internal pullup. 
  
  enableXBee(); //enable the XBee pins.
  displayValue(0xF);
  Serial.print("F"); //stop the rover.
 /* for(int jj = 0; jj<16; jj++) {
   displayValue(jj);
  delay(1000); 
  }*/
}

void loop() {
unsigned int value = getPins();
 switch(value) {
  case 0: if(robotState != 0) { } robotState = 0; break; //no buttons
  case 1: if(robotState != 1) { Serial.print("W"); displayValue(1); } robotState = 1; break; //button 0 = stop
  case 2: if(robotState != 2) { Serial.print("F"); displayValue(2); } robotState = 2; break; //button 1 = forward
  case 4: Serial.print("A"); displayValue(4);  while(getPins()==4); Serial.print("F"); break; //button 2 = backward.
  case 8: Serial.print("D"); displayValue(4);  while(getPins()==8); Serial.print("F"); break; //button 2 = backward.
  case 16: if(robotState != 16) { Serial.print("T"); displayValue(0xA); } robotState = 16; break; //button 3 = speed up
  case 32: if(robotState != 32) { Serial.print("Y"); displayValue(0xB); } robotState = 32; break; //button 4 = slow down.
  case 64: Serial.print("U"); displayValue(4);  while(getPins()==64); Serial.print("I"); break; //button 2 = lever switch off.
  default: if(robotState != 0) { Serial.print("F"); displayValue(0); } robotState = 0; break; //unknown combination
 } 
 delay(10);
}

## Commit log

2011-12-18 added various stuff
    [arduino_card.sch, xbee_remote.brd, xbee_remote.sch]
2012-01-12 Added various files, including gerbers
    [xbee_remote.brd, xbee_remote.sch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]
2012-01-26 UNTESTED: 32u4 based remote control
    Schematic, board, and .ino files for a atmega32u4 based XBee remote
    control for the rover.
    [remote_smt.brd, remote_smt.sch]
2012-01-31 Updated through-hole board and schematic
    Changed polygon fill to hatch, fully routed the board to not need
    polygon, just in case, cleaned up the schematic, and added a net list
    to the schematic.
    [xbee_remote.brd, xbee_remote.sch]
2012-01-31 Fixed up SMT version, added some files zipped.
    [remote_smt.brd, remote_smt.sch]
2012-02-02 Made a bunch of changes.
    Most importantly: Switched the lines for Switch 6 and XBee enable, to
    make routing more sensible, and to make reading of switches take a
    single for loop.
    [xbee_remote.brd, xbee_remote.sch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]
2012-02-19 Updated the schematic and board, and updated the writeup immensely.
    [arduino_card.sch, xbee_remote.brd]
2012-04-23 Added a writeup and a PDF of the schematic and board for easier viewing (w/o EAGLE)
2012-04-29 New revision of remote: Added joystick, shifted parts.
    [arduino_card.sch, xbee_remote.brd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]

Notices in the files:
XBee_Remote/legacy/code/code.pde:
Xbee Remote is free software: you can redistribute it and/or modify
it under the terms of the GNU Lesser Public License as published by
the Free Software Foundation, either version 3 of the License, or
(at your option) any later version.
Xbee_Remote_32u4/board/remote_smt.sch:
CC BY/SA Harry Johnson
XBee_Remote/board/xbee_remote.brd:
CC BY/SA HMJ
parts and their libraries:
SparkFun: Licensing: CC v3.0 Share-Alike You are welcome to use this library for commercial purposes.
